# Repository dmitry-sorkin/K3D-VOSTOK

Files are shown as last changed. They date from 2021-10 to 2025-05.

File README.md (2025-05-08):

# K3D VOSTOK

Проект продвинутого крупногабаритного IDEX принтера.

Когда-то проект выкладывался на GitHub. Но после событий 2022 года использовать эту платформу стало небезопасно для проекта. В связи с этим, релизы, моды и багртрекер проекта теперь располагаются на собственном сайте:

- [Релизы](https://forum.k3d.tech/c/vostok-releases/21)
- [Модификации](https://forum.k3d.tech/c/vostok-mods/17)
- [Багтрекер](https://forum.k3d.tech/c/vostok-bugtracker/19)

Возвращение на GitHub не планируется. По крайней мере пока сохраняется возможность блокировки репозитория из-за не зависящих от автора проекта обстоятельств.

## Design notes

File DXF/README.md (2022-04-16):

# DXF Generator

DXF Generator сделан для генерирования DXF чертежей зашивки.

❗ Alpha-test ❗

На данный момент принтер и документация к нему находятся на стадии активного проектирования. Автор не гарантирует вам ничего. Все результаты работы всех калькуляторов, генераторов и т.д. стоит дважды перепроверить перед совершением заказа.

## Контакты:

+ Создатель: Дмитрий Соркин [dbsorkin@gmail.com]
+ Новости проекта: [https://t.me/vostok3dp]
+ Обсуждение проекта: [https://t.me/k3d_vostok]

## Как поучаствовать в проекте?:

Собрать и тестировать. Большая часть багов может быть найдена только при реальной эксплуатации принтера.

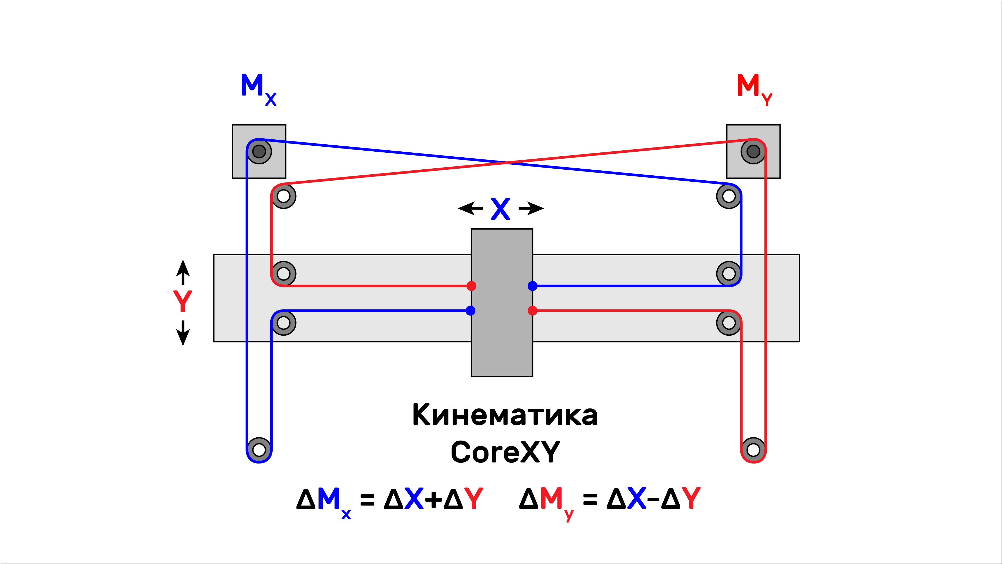
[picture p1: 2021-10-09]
Docs/kinematics_CoreXY.jpg

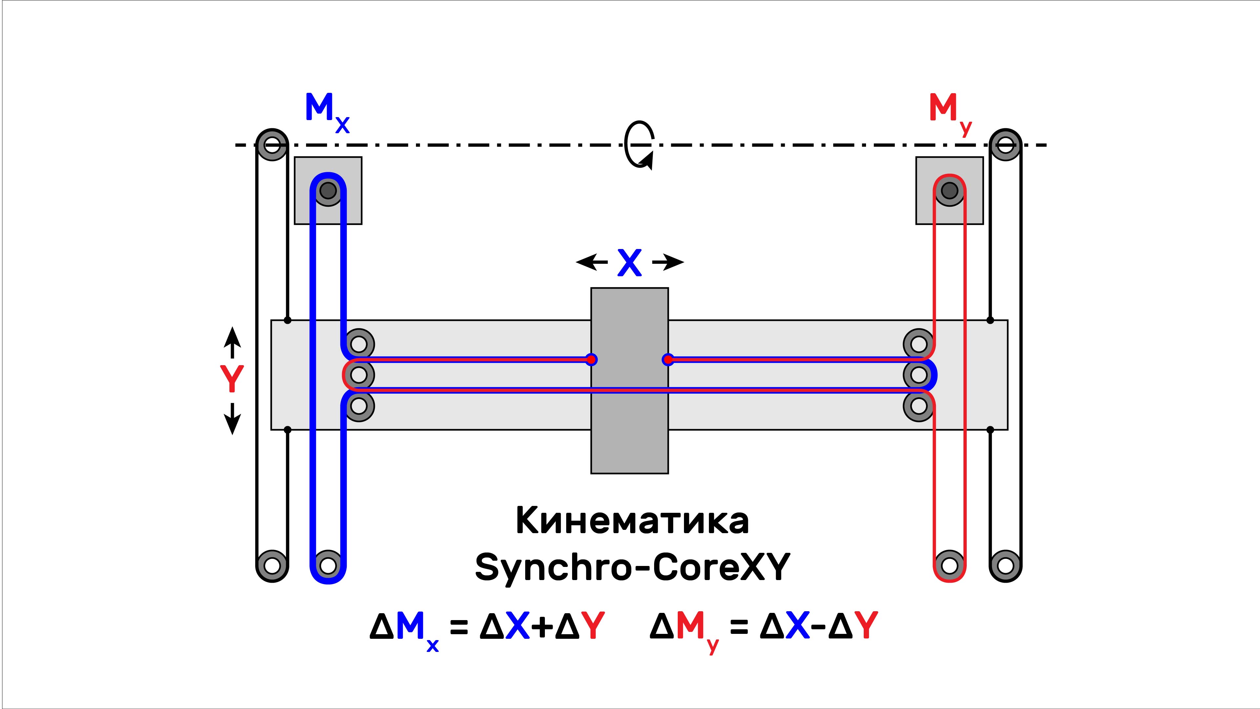
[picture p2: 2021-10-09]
Docs/kinematics_Synchro-CoreXY.jpg

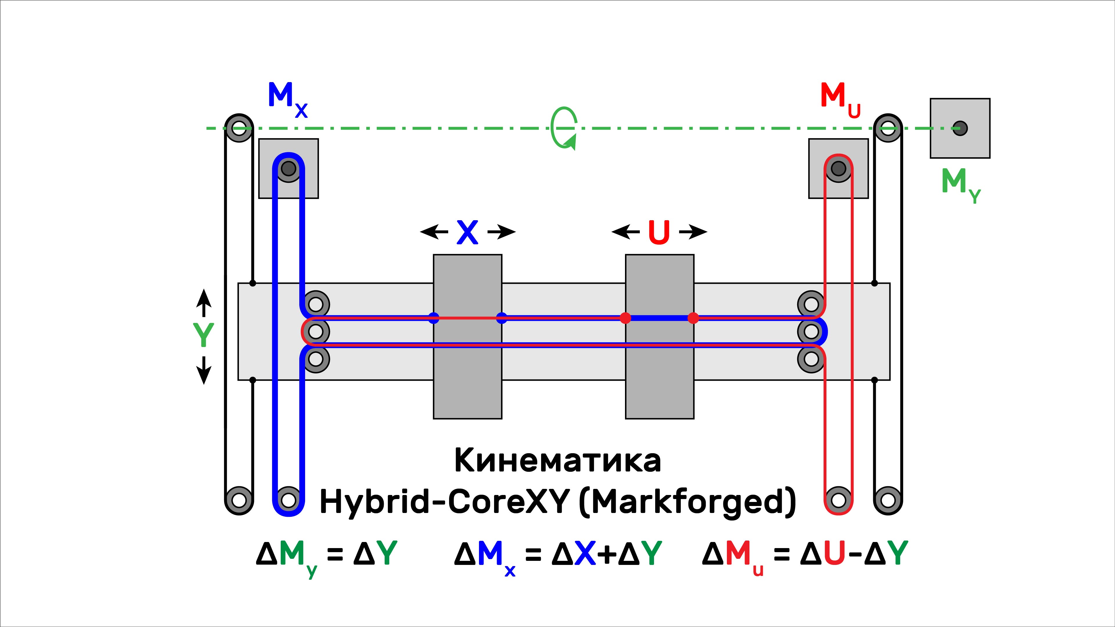
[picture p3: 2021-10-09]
Docs/kinematics_Hybrid-CoreXY.jpg

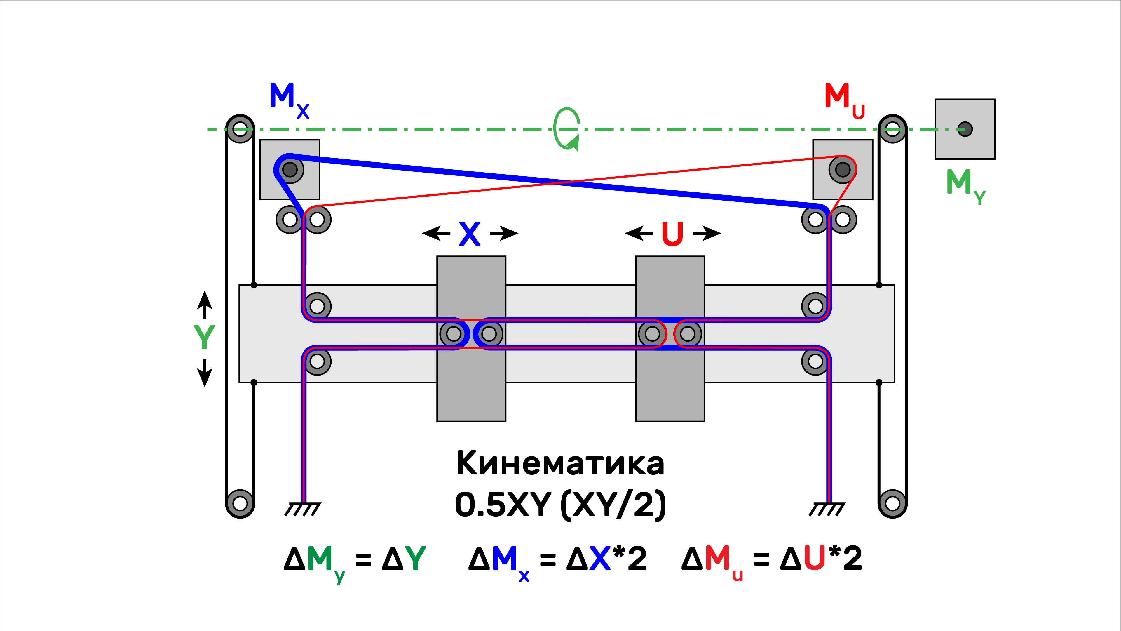
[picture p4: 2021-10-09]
Docs/kinematics_0.5XY.jpg

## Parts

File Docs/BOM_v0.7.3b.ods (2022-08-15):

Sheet: Настройки
Параметр | Значение | Примечание
Экструдер
Количество экструдеров | 2 | 1 — обычный одиночный экструдер. Доступны все кинематики 2 — IDEX. Доступны кинематики 0.5XY и Hybrid-CoreXY
Подающий механизм | K3D Minifeeder | Легкий и дешевый подающий механизм на основе деталей BMG. Используется в легкой печатающей голове (lightweight print head)
Хотэнд | Высокопроизводительный | Простой и дешевый универсальный хотэнд на основе хитблока E3D Volcano. Макс. Объёмный расход до 20-22мм³/с.
Ось Z
Желаемая область печати по Х | 400 мм | Определяет размер плиты стола и полный размер области печати по оси Х в миллиметрах
Желаемая область печати по Y | 250 мм | Определяет размер области печати по оси Y. Обратите внимание, что ввиду конструктивных особенностей принтера, размер плиты должен быть больше на 50мм (это будет автоматически расчитано на листе «покупные изделия»). Припуск в 50мм нужен для расположения крепежных отверстий, прищепок стекла, а также совместимости разных печатающих голов между собой.
Желаемая область печати по Z | 250 мм | Желаемая высота области печати по оси Z в миллиметрах. Реальный размер области печати будет немного больше для обеспечения ровного размера ходового винта
Количество точек крепления стола | 6 | Количество подпружиненных точек крепления стола. Для вариантов с 2 стойками Z доступно либо 4, либо 6 точек. Для вариантов с 4 стойками доступно 4, 6, 8 и 9 точек
Количество стоек оси Z | 2 | Количество стоек и приводов оси Z зависит от габарита области печати, но по желанию может быть скорректировано. Рекомендуется: При Y меньше 300 мм: 2 стойки и 2 привода При Y от 300 до 400 мм: 4 стойки и 2 привода При Y больше 400 мм: 4 стойки и 4 привода
Количество приводов оси Z | 2
Электроника
Материнская плата | BTT Octopus | Fysetc Spider, BTT Octopus подходят для всех версий VOSTOK и являются рекомендуемыми платами BTT Octopus Pro подходит для всех версий и рекомендуется для установки высоковольтных драйверов BTT SKR 3 подходит только для одноэкструдерной версии
Управляющая плата | Orange Pi 3 LTS | Управляющая плата для установки прошивки Klipper. Наиболее оптимальным вариантом по сочетанию цена/характеристики является Orange Pi 3 LTS
Печатные детали
Плотность филамента для несущих деталей | 1,08 г/см³ | Характеристики филамента, который будет использоваться для печати нагруженных деталей механики принтера (каретки, детали печатающей головы и т. д.). Рекомендуется использовать прочный, жесткий, термостойкий и хорошо спекающийся материал. Например: PP GF; PP GF30; PA12 GF30; PA6 GF30 и подобные. Плотность указывается в г/см³, цена в $/кг.
Стоимость филамента для несущих деталей | 2 700,00 ₽ | Стоимость килограмма филамента, из которого будут печататься основные несущие детали принтера
Плотность филамента для вспомогательных деталей | 1,28 г/см³ | Характеристики филамента, который будет использоваться для печати вспомогательных деталей (петли, держатели катушек и т. д.). Рекомендуется прочный, дешевый и легкий в печати филамент с термостойкостью от 70 градусов. Идеальным выбором будет PETG, но возможна замена. Плотность указывается в г/см³, цена в $/кг.
Стоимость филамента для вспомогательный деталей | 1 200,00 ₽ | Стоимость килограмма филамента, из которого будут печататься основные несущие детали принтера
Константы
Курс доллара | 60,00 ₽
Курс доллара Aliexpress | 68,00 ₽ | Используется для примерной корректировки стоимости деталей, покупаемых с Aliexpress
Вывод: Габариты принтера
Габарит принтера по X | 678 мм | Учтена толщина зашивки 4мм, купол и дверца отсека электроники. Не учтены головки винтов и дополнительное внешнее оборудование (внешние держатели катушек и т. д.)
Габарит принтера по Y | 504 мм
Габарит принтера по Z | 698 мм
Вывод: Стоимость
Покупные изделия | 34 442,40 ₽ | С рельсами KGT, для всех товаров не учтена стоимость доставки
Стандартные изделия | 7 360,02 ₽ | Самые дешевые винты, но качественные подшипники
Алюминиевый профиль | 5 993,16 ₽ | Учтен облегченный профиль. В случае использования полнотелого профиля цена выше на ~20%
Печатные детали | 3 069,83 ₽ | Без учёта вспомогательных структур

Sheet: Покупные изделия
На данном листе производится расчёт количества нестандартных деталей Ссылки указаны на проверенные товары с хорошим качеством. Единственное исключение — рельсы MGN9, MGN12 и каретки к ним. Так как качественные рельсы (HIWIN и т. п.) не продаются на Aliexpress, то указаны ссылки на значительно более дешевые KGT. У многих пользователей эти рельсы работают нормально, но в целом количество брака достаточно велико. Поэтому рекомендуется заказывать рельсы HIWIN у официального поставщика в вашем регионе. Ссылки на большую часть товаров являются аффилиативными. Покупая по ним вы поддерживаете проект.
Наименование | Удельная стоимость | Длина/площадь | Единиц | Общая стоимость | Ссылки | Альт. Ссылка | Примечание
Экструдер
Подающий механизм
Клон BMG | 622,00 ₽ |  | 2 | 1 244,00 ₽ | AE (http://alii.pub/6fdbrk) |  | Либо используется как есть, либо служит донором деталей для BeMeGe или Minifeeder
LGX Lite | 3 420,00 ₽ |  | 0 | 0,00 ₽ | BTech (https://www.bondtech.se/product/lgx-lite-extruder-no-motor/) |  | На данный момент продаётся только в Швеции. Если не можете купить, то рекомендуется замена на Minifeeder
Matrix Lite | 5 662,00 ₽ |  | 0 | 0,00 ₽ | AE (http://alii.pub/6fdbp1) |  | Идёт в комплекте с мотором, хитблоком v6, медным соплом v6, термистором, нагревательным элементом и вентилятором
Мотор Nema17 20-23мм | 672,00 ₽ |  | 0 | 0,00 ₽ | AE (http://alii.pub/6fdbno) |  | Для вариантов с BMG или BeMeGe. 1.8 градуса/шаг, любой производитель, любой удобный вам тип проводки
Мотор Nema14 20мм | 1 440,00 ₽ |  | 2 | 2 880,00 ₽ | AE (http://alli.pub/6fdf35) |  | Для вариантов с LGX Lite или Minifeeder. Обязательна запрессованная на вал мотора 10-зубая шестерня. Избегайте моторов 17мм так как у них не хватает крутящего момента, что ведёт к уменьшению производительности экструдера на ~10%
Хотэнд | 0,00 ₽
Радиатор e3d v6 | 83,00 ₽ |  | 0 | 0,00 ₽ | AE (http://alii.pub/6fdbsj) |  | Для головы с BMG используется как есть. Для облегченной печатающей головы необходима доработка
Радиатор CR-10 | 155,00 ₽ |  | 2 | 310,00 ₽ | AE (http://alii.pub/6fdbv2) |  | Используется для сборки в IDEX так как имеет регулировку сопла по высоте
Термобарьер e3d v6 биметалл | 266,00 ₽ |  | 0 | 0,00 ₽ | AE (http://alii.pub/6fdblx) |  | Титановый цельнометаллический как оптимум цена/качество. Биметалл сталь+медь для максимальных характеристик
Термобарьер CR-10 биметалл | 266,00 ₽ |  | 2 | 532,00 ₽ | AE (http://alii.pub/6fdblx) |  | Цельнометаллический титановый нельзя так как эффективности радиатора не хватит. Только биметалл
Хитблок e3d v6 | 88,00 ₽ |  | 0 | 0,00 ₽ | AE (http://alii.pub/6f67wx) |  | Алюминиевые хитблоки — оптимум по цена/масса/качество. Медные, латунные и так далее не нужны. Обратите внимание, что если хитблок включен в комплект поставки экструдера или хотэнда, то покупать его не надо
Хитблок e3d volcano | 149,00 ₽ |  | 2 | 298,00 ₽ | AE (http://alii.pub/6fdbl5)
Хитблок CHC Pro | 1 525,00 ₽ |  | 0 | 0,00 ₽ | AE (http://alii.pub/6fdbw8) |  | Медно-керамический хитблок с повышенной производительностью. Имеет встроенный нагреватель и термистор
Сопло e3d v6 | 205,00 ₽ |  | 0 | 0,00 ₽ | AE (http://alii.pub/6fdbq0) | AE (http://alii.pub/6fdbq7) | Для печати монофиламентами лучше всего латунные сопла. Для печати композитами закалённые стальные
Сопло e3d volcano | 155,00 ₽ |  | 2 | 310,00 ₽ | AE (http://alii.pub/6f6ep5) | AE (http://alii.pub/6fdbkd)
Термистор | 144,00 ₽ |  | 2 | 288,00 ₽ | AE (http://alii.pub/6f67vr) |  | Для печати до 300°C лучше всего 104GT-2. Для печати на температурах выше 300°C — pt100, pt1000 и подобные
Нагревательный элемент 24в 40Вт | 130,00 ₽ |  | 2 | 260,00 ₽ | AE (http://alli.pub/6fdf1z) |  | Для обычных хотэндов 40Вт нагреватель безопаснее всего так как он не может расплавить хитблок.
Система охлаждения | 0,00 ₽
Вентилятор 5015 12-24в | 287,50 ₽ |  | 4 | 1 150,00 ₽ | AE (http://alli.pub/6fdf5h) |  | Вентилятор должен обязательно поддерживать ШИМ, иначе не будет возможности регулировать охлаждение
Вентилятор 4010 12-24в | 299,00 ₽ |  | 2 | 598,00 ₽ | DNS (https://www.dns-shop.ru/product/4a841272207ce478/ventilator-deepcool-xfan-40-dp-fdc-xf40/) | DNS (https://www.dns-shop.ru/product/dc21803bc4a23332/ventilator-fractal-design-silent-series-r3-40-fd-fan-ssr3-40-wt/)
Вентилятор 4007 12-24в | 390,00 ₽ |  | 0 | 0,00 ₽ | AE (http://alli.pub/6fdgoi) |  | Может быть заменен на 4010 вентилятор, но немного уменьшится область печати
Трубка PTFE ID2 OD4 | 0,20 ₽ | 630 мм | 2 | 252,00 ₽ | AE (http://alli.pub/6fdgs0) |  | Для подвода прутка от катушек к экструдерам и сборки хотэнда. Длина расчитана грубо, брать с запасом
Магнит D10 L1 | 8,25 ₽ |  | 0 | 0,00 ₽ | MM (https://mirmagnitov.ru/product/neodimovyy-magnit-disk-10kh1-mm-s-kleevym-sloem/) |  | Для крепления вентилятора обдува модели к каретке старой печатной головы. Можно заменить соединение на клеевое
Ось X | 0,00 ₽
Рельса MGN9 | 1,12 ₽ | 520 мм | 1 | 582,40 ₽ | AE (http://alli.pub/6fdguc) |  | Цена и ссылка указаны на рельсы KGT, имеющие случайное качество. Рекомендуется покупать рельсы HIWIN у официального поставщика в вашем регионе
Каретка MGN9H | 363,00 ₽ |  | 2 | 726,00 ₽ | AE (http://alli.pub/6fdguc)
Мотор Nema17; 38-60мм | 755,00 ₽ |  | 2 | 1 510,00 ₽ | AE (http://alli.pub/6fdh0r) |  | На принтер со столом 400х250 мотора 38мм хватает с запасом. На очень большие принтеры можно взять мотор больше
Шкив 2GT; вн.диам. 5 мм; 20 зубов | 274,00 ₽ |  | 2 | 548,00 ₽ | AE (http://alli.pub/6fdh4g)
Ремень 2GT; 9-10мм | 0,17 ₽ | 2910 мм | 2 | 960,30 ₽ | AE (http://alii.pub/6fdbfp) |  | Указана длина одного куска и количество таких кусков. Размер расчитывается грубо, обязательно брать с запасом
Ось Y | 0,00 ₽
Рельса MGN12 | 1,38 ₽ | 300 мм | 2 | 828,00 ₽ | AE (http://alli.pub/6fdguc) |  | Цена и ссылка указаны на рельсы KGT, имеющие случайное качество. Рекомендуется покупать рельсы HIWIN у официального поставщика в вашем регионе
Каретка MGN12H | 424,00 ₽ |  | 2 | 848,00 ₽ | AE (http://alli.pub/6fdguc)
Мотор Nema17; 38-60мм | 755,00 ₽ |  | 1 | 755,00 ₽ | AE (http://alli.pub/6fdh0r) |  | На принтер со столом 400х250 мотора 38мм хватает. На очень большие принтеры можно взять мотор больше
Вал диаметр 8 мм | 0,80 ₽ | 620 мм | 1 | 496,00 ₽ | AE (http://alli.pub/6fdhks)
Шкив 2GT; вн.диам. 5 мм; 20 зубов | 274,00 ₽ |  | 1 | 274,00 ₽ | AE (http://alli.pub/6fdh4g)
Шкив 2GT; вн.диам. 8 мм; 20 зубов | 274,00 ₽ |  | 3 | 822,00 ₽ | AE (http://alli.pub/6fdh4g)
Ремень 2GT; 9-10мм; открытый | 0,17 ₽ | 740 мм | 2 | 244,20 ₽ | AE (http://alii.pub/6fdbfp) |  | Длина ремня расчитывается грубо. Обязательно брать с запасом
Ремень 2GT; 9-10мм; кольцо 150мм (75 зубов) | 480,00 ₽ |  | 1 | 480,00 ₽ | AE (http://alli.pub/6fdhg4)
Ось Z | 0,00 ₽
Каретка Openbuilds в сборе | 296,00 ₽ |  | 2 | 592,00 ₽ | AE (http://alli.pub/6fdhys) |  | Продаётся с 4 колёсами, но нужно только 3. Лишнее в запчасти
Винт Tr8x2 | 1,16 ₽ | 300 мм | 2 | 696,00 ₽ | AE (http://alli.pub/6fdi93) |  | Tr8x2 — однозаходная трапецеидальная резьба. Диаметр = 8мм. Ход = шаг = 2мм.
Гайка POM Tr8x2 | 114,00 ₽ |  | 2 | 228,00 ₽ | AE (http://alli.pub/6fdid6) |  | Tr8x2 — резьба трапецеидальная с диаметром 8мм и шагом 2мм. Ход равен шагу.
Мотор Nema17; 30-42мм | 755,00 ₽ |  | 2 | 1 510,00 ₽ | AE (http://alli.pub/6fdh0r) |  | Можно поставить моторы длиннее, но придется поднимать принтер на ножках
Муфта жесткая 5x8мм | 93,00 ₽ |  | 2 | 186,00 ₽ | AE (http://alii.pub/6fdb9h) |  | Можно заменить на кулачковую или печатную
Стол | 0,00 ₽
Лист алюминиевый 400 х 300 х 4 мм | 8 000,00 ₽ | 0,12 м² | 1 | 960,00 ₽ | Prutki (http://prutki.ru/list-alyuminievyj-amg2-tolshchina-4-mm/) |  | Можно заменить на латунь или стеклотекстолит
Грелка силиконовая 400 х 250 мм | 16 700,00 ₽ | 0,1 м² | 1 | 1 670,00 ₽ | AE (http://alli.pub/6fdk03) | AE (http://alli.pub/6fdk4d) | Желательно брать от проверенного проивзодителя ради безопасности
Стекло 400 х 300 х 4 мм | 2 000,00 ₽ | 0,12 м² | 1 | 240,00 ₽ | N/A | N/A | Обычное оконное стекло из ближайшей стеклорезки
Прищепка для стекла | 25,00 ₽ |  | 4 | 100,00 ₽ | AE (http://alli.pub/6fdkaz)
Пружина OD8 L25 | 12,00 ₽ |  | 6 | 72,00 ₽ | AE (http://alli.pub/6fdosk)
Электроника | 0,00 ₽
Блок питания 24в 200Вт | 2 250,00 ₽ |  | 1 | 2 250,00 ₽ | CD (https://www.chipdip.ru/product/lrs-200-24) |  | Качественный блок питания с пассивным охлаждением
Блок питания 24в 350Вт | 3 340,00 ₽ |  | 0 | 0,00 ₽ | CD (https://www.chipdip.ru/product/lrs-350-24) |  | Качественный блок питания с активным и шумным охлаждением. Придётся менять вентилятор в нём на тихий
Блок питания 5в 25Вт | 940,00 ₽ |  | 0 | 0,00 ₽ | CD (https://www.chipdip.ru/product/rs-25-5) |  | На случай, если 5в линии питания материнской платы не будет хватать для питания управляющей платы
Вентилятор 90-120 мм 12 в | 389,00 ₽ |  | 0 | 0,00 ₽ | DNS (https://www.dns-shop.ru/product/0b8ea57aad253332/ventilator-xilence-xf038-xpf92r/) |  | Для замены вентилятора в блоке питания LRS-350
Fysetc Spider + 8x tmc2209 | 4 600,00 ₽ |  | 0 | 0,00 ₽ | AE (http://alli.pub/6fdksh)
BTT Octopus + 8x tmc2209 | 4 234,00 ₽ |  | 1 | 4 234,00 ₽ | AE (http://alli.pub/6fdkrb)
BTT Octopus Pro + 8x tmc2209 | 5 775,00 ₽ |  | 0 | 0,00 ₽ | AE (http://alli.pub/6fdkn8)
BTT SKR 1.4 + 5x tmc2209 | 3 270,00 ₽ |  | 0 | 0,00 ₽ | AE (http://alli.pub/6fdkn8)
Orange Pi Lite | 1 853,00 ₽ |  | 0 | 0,00 ₽ | AE (http://alli.pub/6fdkvl)
Orange Pi 3 LTS | 2 403,00 ₽ |  | 1 | 2 403,00 ₽ | AE (http://alii.pub/6fdbj0)
Orange Pi 4 LTS | 5 005,00 ₽ |  | 0 | 0,00 ₽ | AE (http://alli.pub/6fdkum)
Карта памяти microSD 16Gb | 599,00 ₽ |  | 1 | 599,00 ₽ | DNS (https://www.dns-shop.ru/product/b7ef4eb6147c3332/karta-pamati-smartbuy-microsdhc-8-gb-sb8gbsdcl10-00/)
Реле твердотельное 25А | 195,00 ₽ |  | 1 | 195,00 ₽ | AE (http://alli.pub/6fdkwk)
Концевик оптический | 62,00 ₽ |  | 2 | 124,00 ₽ | AE (http://alli.pub/6fdkg8)
Концевик механический | 9,50 ₽ |  | 2 | 19,00 ₽ | AE (http://alli.pub/6fdkwy) |  | С лапкой со скруглением или роликом на конце. Если не хотите использовать sensorless homing на оси Y, то добавьте еще 2
Розетка 250В | 153,00 ₽ |  | 1 | 153,00 ₽ | AE (http://alli.pub/6fdkdi)
Зашивка и навесное | 0,00 ₽
Вентилятор 200мм | 999,00 ₽ |  | 1 | 999,00 ₽ | DNS (https://www.dns-shop.ru/product/da7f8125c4923332/ventilator-aerocool-duo-20/)
Магнит D10 L1 | 8,25 ₽ |  | 2 | 16,50 ₽ | MM (https://mirmagnitov.ru/product/neodimovyy-magnit-disk-10kh1-mm-s-kleevym-sloem/)
Итого: |  |  |  | 34 442,40 ₽

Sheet: Стандартные изделия
 |  |  |  |  |  |  |  | Наименование сборки | K3D VOSTOK | XY portal | X axis | Y axis carriage | Roller | BMG print head | Matrix print head | Lite print head | X axis drive | Y axis drive | Left belt tensioner | Belt tensioner (roller) | Belt tensioner (fixed) | Right belt tensioner | X axis mechanical endstop | Y axis mechanical endstop | Lower frame | Z axis | Z axis guide | Z axis drive | Heatbed frame | Bed arm | Heatbed install | Optical endstop install | Optical endstop trigger | Quad guide nut install | Enclosure | Front door | Enclosure hinge | Back door | Back door lock | Electronics | Additions | Inner spool holder | Inner spool holder rocker | Enclosure top | Enclosure top hinge
 |  |  |  |  |  |  |  | Ед. | 1 | 1 | 1 | 2 | 19 | 0 | 0 | 2 | 2 | 1 | 1 | 2 | 2 | 1 | 2 | 1 | 1 | 1 | 2 | 2 | 1 | 3 | 1 | 1 | 1 | 0 | 1 | 2 | 6 | 1 | 2 | 1 | 1 | 2 | 4 | 2 | 2
Наименование | Стандарт | Резьба | Цена/ед. | Кол-во | Цена всего | Ссылки | Ссылка
Винт с полукруглой головкой и шестигранным углублением под ключ | ISO 7380-1 | М3х6 | 3,00 ₽ | 172 | 516,00 ₽ | krepcom (https://krepcom.ru/catalog/vinty-razdel/vint_3kh6_s_polukrugloy_golovkoy_i_vnutrennim_shestigrannikom_din_7380_nerzh_stal_a2.htm) | krep-shop (https://krep-shop.ru/katalog/bolty_i_vinty/iso_7380_1/3kh6_v_sh_p_kr_nerzh_a2_iso_7380/) |  |  |  |  | 2 |  | 4 | 10 | 6 | 3 | 8 |  |  |  |  |  |  |  |  |  |  |  |  |  |  | 2 |  |  | 2 |  |  |  |  |  |  |  | 68
 | ISO 7380-1 | М3х12 | 3,00 ₽ | 14 | 42,00 ₽ | krepcom (https://krepcom.ru/catalog/vinty-razdel/vint_3kh12_s_polukrugloy_golovkoy_i_vnutrennim_shestigrannikom_din_7380_nerzh_stal_a2.htm) | krep-shop (https://krep-shop.ru/katalog/bolty_i_vinty/iso_7380_1/3kh12_v_sh_p_kr_nerzh_a2_iso_7380/) |  |  |  |  |  |  |  |  | 2 |  |  |  |  |  |  |  |  |  |  |  | 4 |  |  |  |  |  | 4 |  |  |  |  | 1
 | ISO 7380-1 | М3х16 | 4,00 ₽ | 0 | 0,00 ₽ | krepcom (https://krepcom.ru/catalog/vinty-razdel/vint_3kh16_s_polukrugloy_golovkoy_i_vnutrennim_shestigrannikom_din_7380_nerzh_stal_a2.htm) | krep-shop (https://krep-shop.ru/katalog/bolty_i_vinty/iso_7380_1/3kh16_v_sh_p_kr_nerzh_a2_iso_7380/) |  |  |  |  |  |  | 2
 | ISO 7380-1 | М4х8 | 5,00 ₽ | 47 | 235,00 ₽ | krepcom (https://krepcom.ru/catalog/vinty-razdel/vint_4kh8_s_polukrugloy_golovkoy_i_vnutrennim_shestigrannikom_din_7380_nerzh_stal_a2.htm) | krep-shop (https://krep-shop.ru/katalog/bolty_i_vinty/iso_7380_1/4kh8_v_sh_p_kr_nerzh_a2_iso_7380/) |  |  |  |  |  |  |  |  |  | 4 | 8 | 4 |  |  | 4 | 2 | 1 |  |  |  |  |  | 6
 | ISO 7380-1 | М4х12 | 5,00 ₽ | 22 | 110,00 ₽ | krepcom (https://krepcom.ru/catalog/vinty-razdel/vint_4kh12_s_polukrugloy_golovkoy_i_vnutrennim_shestigrannikom_din_7380_nerzh_stal_a2.htm) | krep-shop (https://krep-shop.ru/katalog/bolty_i_vinty/iso_7380_1/4kh12_v_sh_p_kr_nerzh_a2_iso_7380/) |  |  |  |  |  |  |  |  |  |  |  |  |  |  |  |  |  |  |  | 3 | 2 |  |  |  |  |  |  |  |  |  |  |  |  |  | 4 |  | 2
 | ISO 7380-1 | М6х12 | 7,00 ₽ | 42 | 294,00 ₽ | krepcom (https://krepcom.ru/catalog/vinty-razdel/vint_6kh12_s_polukrugloy_golovkoy_i_vnutrennim_shestigrannikom_din_7380_nerzh_stal_a2.htm) | krep-shop (https://krep-shop.ru/katalog/bolty_i_vinty/iso_7380_1/6kh12_v_sh_p_kr_nerzh_a2_iso_7380/) |  | 34 |  |  |  |  |  |  |  |  |  |  |  |  |  |  |  | 4 |  |  |  |  |  |  |  |  |  | 4
-||- с прессшайбой | ISO 7380-2 | М4х8 | 3,00 ₽ | 201 | 603,00 ₽ | krepcom (https://krepcom.ru/catalog/vinty-razdel/vint_4kh8_s_polukrugloy_golovkoy_i_flantsem_9335_nerzh_stal_a2.htm) | krep-shop (https://krep-shop.ru/katalog/bolty_i_vinty/iso_7380w/4kh8_v_sh_p_kr_i_flanets_nerzh_a2_iso_7380_mf/) |  |  |  |  |  |  |  |  |  |  |  |  |  |  |  |  |  |  |  |  |  |  |  |  |  |  |  | 201
Винт с потайной головкой и шестигранным углублением под ключ | DIN 7991 | М3х6 | 3,00 ₽ | 16 | 48,00 ₽ | krepcom (https://krepcom.ru/catalog/vinty-razdel/vint_3kh6_potay_s_vnutrennim_shestigrannikom_nerzhaveyka.htm) | krep-shop (https://krep-shop.ru/katalog/bolty_i_vinty/din_7991/3kh6_pot_v_sh_nerzh_a2_din_7991/) |  |  |  |  | 4 |  |  |  | 4
 | DIN 7991 | М3х12 | 3,00 ₽ | 16 | 48,00 ₽ | krepcom (https://krepcom.ru/catalog/vinty-razdel/vint_3kh12_potay_s_vnutrennim_shestigrannikom_nerzhaveyka.htm) | krep-shop (https://krep-shop.ru/katalog/bolty_i_vinty/din_7991/3kh12_pot_v_sh_nerzh_a2_din_7991/) |  |  |  |  | 2 |  |  |  |  |  |  |  |  |  |  |  |  |  |  |  |  |  |  |  |  |  |  |  |  | 2
 | DIN 7991 | М3х16 | 4,00 ₽ | 13 | 52,00 ₽ | krepcom (https://krepcom.ru/catalog/vinty-razdel/vint_potay_s_vnutrennim_shestigrannikom_m3kh16_din_7991_iso_10642_klass_prochnosti_10_9_otsinkovanny.htm) | krep-shop (https://krep-shop.ru/katalog/bolty_i_vinty/din_7991/3kh16_pot_v_sh_nerzh_a2_din_7991/) |  |  |  |  |  |  |  |  |  |  | 1 |  |  |  |  |  |  |  |  |  |  |  |  |  |  |  |  |  |  | 2
 | DIN 7991 | М3х20 | 5,00 ₽ | 8 | 40,00 ₽ | krepcom (https://krepcom.ru/catalog/vinty-razdel/vint_potay_s_vnutrennim_shestigrannikom_m3kh20_din_7991_iso_10642_klass_prochnosti_10_9_otsinkovanny.htm) | krep-shop (https://krep-shop.ru/katalog/bolty_i_vinty/din_7991/3kh20_pot_v_sh_nerzh_a2_din_7991/) |  |  |  |  |  |  |  | 3 |  |  |  |  | 1 |  |  |  |  |  |  |  |  |  |  |  |  |  |  |  |  | 1
 | DIN 7991 | М3х30 | 6,00 ₽ | 6 | 36,00 ₽ | krepcom (https://krepcom.ru/catalog/vinty-razdel/vint_potay_s_vnutrennim_shestigrannikom_3kh30_din_7991_otsinkovannyy.htm) | krep-shop (https://krep-shop.ru/katalog/bolty_i_vinty/din_7991/3kh30_pot_v_sh_nerzh_a2_din_7991/) |  |  |  |  |  |  |  |  |  |  |  |  |  |  |  |  |  |  |  |  |  |  |  |  |  |  |  |  |  |  | 4 |  |  |  |  |  |  | 1
 | DIN 7991 | М3х35 | 6,00 ₽ | 12 | 72,00 ₽ | krepcom (https://krepcom.ru/catalog/vinty-razdel/vint_potay_s_vnutrennim_shestigrannikom_din_7991_3x35_stal_a2.htm) | krep-shop (https://krep-shop.ru/katalog/bolty_i_vinty/din_7991/3kh35_pot_v_sh_nerzh_a2_din_7991/) |  |  |  |  | 2 |  | 2 | 2 | 2 | 2
 | DIN 7991 | М3х50 | 10,00 ₽ | 6 | 60,00 ₽ | krepcom (https://krepcom.ru/catalog/vinty-razdel/vint_potay_3kh50_stal_a2.htm) | krep-shop (https://krep-shop.ru/katalog/bolty_i_vinty/din_7991/3kh50_pot_v_sh_nerzh_a2_din_7991/) |  |  |  |  |  |  |  |  |  |  |  |  |  |  |  |  |  |  |  |  |  |  |  | 6
 |  | М4х8 | 3,00 ₽ | 29 | 87,00 ₽ | krepcom (https://krepcom.ru/catalog/vinty-razdel/vint_potay_s_vnutrennim_shestigrannikom_m4kh8_din_7991_iso_10642_klass_prochnosti_10_9_otsinkovannyy.htm) | krep-shop (https://krep-shop.ru/katalog/bolty_i_vinty/din_7991/4kh8_pot_v_sh_nerzh_a2_din_7991/) |  |  |  |  |  |  |  |  |  | 2 | 4 |  |  |  |  |  |  |  |  | 6 |  |  | 2 |  | 3 |  | 4
 |  | М4х12 | 4,00 ₽ | 8 | 32,00 ₽ | krepcom (https://krepcom.ru/catalog/vinty-razdel/vint_potay_s_vnutrennim_shestigrannikom_m4kh12_din_7991_iso_10642_klass_prochnosti_10_9_otsinkovanny.htm) | krep-shop (https://krep-shop.ru/katalog/bolty_i_vinty/din_7991/4kh12_pot_v_sh_nerzh_a2_din_7991/) |  |  |  |  | 2 |  |  |  |  |  |  |  |  |  |  |  |  |  |  |  | 2
 |  | М5х12 | 4,00 ₽ | 24 | 96,00 ₽ | krepcom (https://krepcom.ru/catalog/vinty-razdel/vint_potay_5kh12_s_vnutrennim_shestigrannikom_otsinkovannyy.htm) | krep-shop (https://krep-shop.ru/katalog/bolty_i_vinty/din_7991/5kh12_pot_v_sh_nerzh_a2_din_7991/) |  |  |  |  |  |  |  |  |  |  |  |  |  |  |  |  |  |  |  |  |  |  |  |  |  |  |  |  |  |  |  |  |  |  |  | 6
 |  | М5х16 | 5,00 ₽ | 2 | 10,00 ₽ | krepcom (https://krepcom.ru/catalog/vinty-razdel/vint_potay_s_vnutrennim_shestigrannikom_m5kh16_din_7991_iso_10642_klass_prochnosti_10_9_otsinkovanny.htm) | krep-shop (https://krep-shop.ru/katalog/bolty_i_vinty/din_7991/5kh16_pot_v_sh_nerzh_a2_din_7991/) |  |  |  |  |  |  |  |  |  |  |  | 1 |  |  | 1
Винт с цилиндрической головкой и шестигранным углублением под ключ | DIN 912 | М2.5х8 | 5,00 ₽ | 0 | 0,00 ₽ | krepcom (https://krepcom.ru/catalog/bolty-razdel/bolt_vint_s_vnutrennim_shestigrannikom_i_tsilindricheskoy_golovkoy_din_912_2_5kh8_nerzhaveyka_a4.htm) | krep-shop (https://krep-shop.ru/katalog/bolty_i_vinty/din_912/2_5kh8_v_sh_nerzh_a2_din_912/) |  |  |  |  |  |  |  |  | 0
 |  | М3х8 | 2,00 ₽ | 56 | 112,00 ₽ | krepcom (https://krepcom.ru/catalog/vinty-razdel/vint_s_vnutrennim_shestigrannikom_3kh8_din_912_klass_10_9_otsinkovannyy.htm) | krep-shop (https://krep-shop.ru/katalog/bolty_i_vinty/din_912/3kh8_v_sh_nerzh_a2_din_912/) |  |  | 20 | 26 |  |  |  |  |  |  |  |  |  |  |  |  |  |  |  |  | 4 |  |  |  | 2
 |  | М3х20 | 5,00 ₽ | 10 | 50,00 ₽ | krepcom (https://krepcom.ru/catalog/bolty-razdel/bolt_imbus_3h20_nerj_DIN_912__stal__a2.htm) | krep-shop (https://krep-shop.ru/katalog/bolty_i_vinty/din_912/3kh20_v_sh_nerzh_a2_din_912/) |  |  |  |  |  |  |  |  | 2 |  | 2 |  |  | 2
 |  | М3х40 | 8,00 ₽ | 0 | 0,00 ₽ | krepcom (https://krepcom.ru/catalog/vysokoprochnyy_krepezh_12_9/vint_s_tsilindricheskoy_golovkoy_i_vnutrennim_shestigrannikom_din_912_3x40_vysokoprochnyy_12_9.htm) | krep-shop (https://krep-shop.ru/katalog/bolty_i_vinty/din_912/3kh40_v_sh_nerzh_a2_din_912/) |  |  |  |  |  |  | 3
 |  | М5х16 | 4,00 ₽ | 2 | 8,00 ₽ | krepcom (https://krepcom.ru/catalog/bolty-razdel/vint_bolt_din_912_m5kh16_klass_prochnosti_8_8.htm) | krep-shop (https://krep-shop.ru/katalog/bolty_i_vinty/din_912/5kh16_v_sh_nerzh_a2_din_912/) |  |  |  |  |  |  |  |  |  |  |  |  |  | 1
Болт | DIN 933 | М5х50 | 4,00 ₽ | 4 | 16,00 ₽ | krepcom (https://krepcom.ru/catalog/bolty-razdel/bolt_shestigrannyy_5kh50_din_933_klass_prochnosti_8_8_otsinkovannyy.htm) | krep-shop (https://krep-shop.ru/katalog/bolty_i_vinty/din_933/5kh50_nerzh_a2_din_933/) |  |  |  |  |  |  |  |  |  |  |  |  | 1 | 1
Гайка шестигранная | DIN 934 | М3 | 2,00 ₽ | 56 | 112,00 ₽ | krepcom (https://krepcom.ru/catalog/gayki-razdel/gayka_sh_gr_m_3_DIN_934_ots.htm) | krep-shop (https://krep-shop.ru/katalog/gaiki/din_934/m3_nerzh_a_2_din_934/) |  |  |  |  | 4 |  | 6 | 2 |  | 2 |  |  |  |  |  |  |  |  |  |  |  |  |  | 6 |  |  |  |  |  | 4 | 4 |  |  |  |  |  |  | 5
 |  | М4 | 2,00 ₽ | 6 | 12,00 ₽ | krepcom (https://krepcom.ru/catalog/gayki-razdel/gayka_sh_gr_m_4_DIN_934_ots.htm) | krep-shop (https://krep-shop.ru/katalog/gaiki/din_934/m4_nerzh_a_2_din_934/) |  |  |  |  |  |  |  |  |  |  |  |  |  |  |  |  |  |  |  | 3
 |  | М5 | 2,00 ₽ | 4 | 8,00 ₽ | krepcom (https://krepcom.ru/catalog/gayki-razdel/gayka_vysokoprochnaya_m5_din_934_klass_10_otsinkovannaya.htm) | krep-shop (https://krep-shop.ru/katalog/gaiki/din_934/m5_nerzh_a_2_din_934/) |  |  |  |  |  |  |  |  |  |  |  |  | 1 | 1
Т-гайка |  | М3 | 5,90 ₽ | 46 | 271,40 ₽ |  | AE (https://aliclick.shop/s/98tdf1) |  |  | 20 | 26
 |  | М4 | 5,90 ₽ | 283 | 1 669,70 ₽ |  | AE (https://aliclick.shop/s/98tdf1) |  |  |  |  | 2 |  |  |  |  | 4 | 12 | 4 |  |  | 4 | 2 | 1 |  |  | 6 | 3 |  | 8 |  | 3 |  | 4 | 201
Резьбовая вставка |  | М3х3 | 1,02 ₽ | 8 | 8,16 ₽ |  | AE (https://aliclick.shop/s/wmicc9) |  |  |  |  |  |  |  |  | 4
 |  | М3х5 | 2,23 ₽ | 22 | 49,06 ₽ |  | AE (https://aliclick.shop/s/wmicc9) |  |  |  |  |  |  |  |  | 8 |  |  |  |  |  |  |  |  |  |  |  |  |  |  | 6
Шайба | DIN 125 | М3 | 2,00 ₽ | 0 | 0,00 ₽ | krepcom (https://krepcom.ru/catalog/shayby/shayba-ploskaya-m3-din-125a-stal-nikelirovannaya.htm) | krep-shop (https://krep-shop.ru/katalog/shaiby/din_125/f3_2_m3_pl_nerzh_a2_din_125/)
 |  | М4 | 2,00 ₽ | 6 | 12,00 ₽ | krepcom (https://krepcom.ru/catalog/shayby/shayba-ploskaya-m4-din-125a-stal-nikelirovannaya.htm) | krep-shop (https://krep-shop.ru/katalog/shaiby/din_125/f4_3_m4_pl_nerzh_a2_din_125/) |  |  |  |  |  |  |  |  |  |  |  |  |  |  |  |  |  |  |  | 3
 |  | М8 | 2,00 ₽ | 3 | 6,00 ₽ | krepcom (https://krepcom.ru/catalog/shayby/shayba_m__8_prostaya_DIN_125_ots.htm) | krep-shop (https://krep-shop.ru/katalog/shaiby/din_125/f8_4_m8_pl_nerzh_a2_din_125/) |  |  |  |  |  |  |  |  |  |  | 3
Подшипник | 623 (zz или rs) |  | 33,50 ₽ | 19 | 636,50 ₽ |  | AE (https://aliclick.shop/s/ynp7je) |  |  |  |  |  | 1
 | F623 (zz или rs) |  | 31,10 ₽ | 38 | 1 181,80 ₽ |  | AE (https://aliclick.shop/s/fcdz1a) |  |  |  |  |  | 2
 | F695 (zz или rs) |  | 31,30 ₽ | 24 | 751,20 ₽ |  | AE (https://aliclick.shop/s/nh5fvo) |  |  |  |  |  |  |  |  |  |  |  |  |  |  |  |  |  |  |  |  |  |  |  |  |  |  |  |  |  |  |  |  |  |  |  | 6
 | F688 (zz или rs) |  | 37,60 ₽ | 2 | 75,20 ₽ |  | AE (https://aliclick.shop/s/db73tn) |  |  |  |  |  |  |  |  |  |  | 2
Итого: |  |  |  |  | 7 360,02 ₽
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

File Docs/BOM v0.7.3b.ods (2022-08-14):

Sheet: Настройки
Параметр | Значение | Примечание
Экструдер
Количество экструдеров | 2 | 1 — обычный одиночный экструдер. Доступны все кинематики 2 — IDEX. Доступны кинематики 0.5XY и Hybrid-CoreXY
Подающий механизм | K3D Minifeeder | Легкий и дешевый подающий механизм на основе деталей BMG. Используется в легкой печатающей голове (lightweight print head)
Хотэнд | Высокопроизводительный | Простой и дешевый универсальный хотэнд на основе хитблока E3D Volcano. Макс. Объёмный расход до 20-22мм³/с.
Ось Z
Желаемая область печати по Х | 400 мм | Определяет размер плиты стола и полный размер области печати по оси Х в миллиметрах
Желаемая область печати по Y | 250 мм | Определяет размер области печати по оси Y. Обратите внимание, что ввиду конструктивных особенностей принтера, размер плиты должен быть больше на 50мм (это будет автоматически расчитано на листе «покупные изделия»). Припуск в 50мм нужен для расположения крепежных отверстий, прищепок стекла, а также совместимости разных печатающих голов между собой.
Желаемая область печати по Z | 250 мм | Желаемая высота области печати по оси Z в миллиметрах. Реальный размер области печати будет немного больше для обеспечения ровного размера ходового винта
Количество точек крепления стола | 6 | Количество подпружиненных точек крепления стола. Для вариантов с 2 стойками Z доступно либо 4, либо 6 точек. Для вариантов с 4 стойками доступно 4, 6, 8 и 9 точек
Количество стоек оси Z | 2 | Количество стоек и приводов оси Z зависит от габарита области печати, но по желанию может быть скорректировано. Рекомендуется: При Y меньше 300 мм: 2 стойки и 2 привода При Y от 300 до 400 мм: 4 стойки и 2 привода При Y больше 400 мм: 4 стойки и 4 привода
Количество приводов оси Z | 2
Электроника
Материнская плата | BTT Octopus | Fysetc Spider, BTT Octopus подходят для всех версий VOSTOK и являются рекомендуемыми платами BTT Octopus Pro подходит для всех версий и рекомендуется для установки высоковольтных драйверов BTT SKR 3 подходит только для одноэкструдерной версии
Управляющая плата | Orange Pi 3 LTS | Управляющая плата для установки прошивки Klipper. Наиболее оптимальным вариантом по сочетанию цена/характеристики является Orange Pi 3 LTS
Печатные детали
Плотность филамента для несущих деталей | 1,08 г/см³ | Характеристики филамента, который будет использоваться для печати нагруженных деталей механики принтера (каретки, детали печатающей головы и т. д.). Рекомендуется использовать прочный, жесткий, термостойкий и хорошо спекающийся материал. Например: PP GF; PP GF30; PA12 GF30; PA6 GF30 и подобные. Плотность указывается в г/см³, цена в $/кг.
Стоимость филамента для несущих деталей | 2 700,00 ₽ | Стоимость килограмма филамента, из которого будут печататься основные несущие детали принтера
Плотность филамента для вспомогательных деталей | 1,28 г/см³ | Характеристики филамента, который будет использоваться для печати вспомогательных деталей (петли, держатели катушек и т. д.). Рекомендуется прочный, дешевый и легкий в печати филамент с термостойкостью от 70 градусов. Идеальным выбором будет PETG, но возможна замена. Плотность указывается в г/см³, цена в $/кг.
Стоимость филамента для вспомогательный деталей | 1 200,00 ₽ | Стоимость килограмма филамента, из которого будут печататься основные несущие детали принтера
Константы
Курс доллара | 60,00 ₽
Курс доллара Aliexpress | 68,00 ₽ | Используется для примерной корректировки стоимости деталей, покупаемых с Aliexpress
Вывод: Габариты принтера
Габарит принтера по X | 678 мм | Учтена толщина зашивки 4мм, купол и дверца отсека электроники. Не учтены головки винтов и дополнительное внешнее оборудование (внешние держатели катушек и т. д.)
Габарит принтера по Y | 504 мм
Габарит принтера по Z | 698 мм
Вывод: Стоимость
Покупные изделия | 34 442,40 ₽ | С рельсами KGT, для всех товаров не учтена стоимость доставки
Стандартные изделия | 7 360,02 ₽ | Самые дешевые винты, но качественные подшипники
Алюминиевый профиль | 3 915,16 ₽ | Учтен облегченный профиль. В случае использования полнотелого профиля цена выше на ~20%
Печатные детали | 3 069,83 ₽ | Без учёта вспомогательных структур
Проводка |  | Расчёт на данный момент не готов

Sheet: Покупные изделия
На данном листе производится расчёт количества нестандартных деталей Ссылки указаны на проверенные товары с хорошим качеством. Единственное исключение — рельсы MGN9, MGN12 и каретки к ним. Так как качественные рельсы (HIWIN и т. п.) не продаются на Aliexpress, то указаны ссылки на значительно более дешевые KGT. У многих пользователей эти рельсы работают нормально, но в целом количества брака достаточно велико. Поэтому рекомендуется заказывать рельсы HIWIN у официального поставщика в вашем регионе. Ссылки на большую часть товаров являются аффилиативными. Покупая по ним вы поддерживаете проект.
Наименование | Удельная стоимость | Длина/площадь | Единиц | Общая стоимость | Ссылки | Альт. Ссылка | Примечание
Экструдер
Подающий механизм
Клон BMG | 622,00 ₽ |  | 2 | 1 244,00 ₽ | AE (http://alii.pub/6fdbrk) |  | Либо используется как есть, либо служит донором деталей для BeMeGe или Minifeeder
LGX Lite | 3 420,00 ₽ |  | 0 | 0,00 ₽ | BTech (https://www.bondtech.se/product/lgx-lite-extruder-no-motor/) |  | На данный момент продаётся только в Швеции. Если не можете купить, то рекомендуется замена на Minifeeder
Matrix Lite | 5 662,00 ₽ |  | 0 | 0,00 ₽ | AE (http://alii.pub/6fdbp1) |  | Идёт в комплекте с мотором, хитблоком v6, медным соплом v6, термистором, нагревательным элементом и вентилятором
Мотор Nema17 20-23мм | 672,00 ₽ |  | 0 | 0,00 ₽ | AE (http://alii.pub/6fdbno) |  | Для вариантов с BMG или BeMeGe. 1.8 градуса/шаг, любой производитель, любой удобный вам тип проводки
Мотор Nema14 20мм | 1 440,00 ₽ |  | 2 | 2 880,00 ₽ | AE (http://alli.pub/6fdf35) |  | Для вариантов с LGX Lite или Minifeeder. Обязательна запрессованная на вал мотора 10-зубая шестерня. Избегайте моторов 17мм так как у них не хватает крутящего момента, что ведёт к уменьшению производительности экструдера на ~10%
Хотэнд | 0,00 ₽
Радиатор e3d v6 | 83,00 ₽ |  | 0 | 0,00 ₽ | AE (http://alii.pub/6fdbsj) |  | Для головы с BMG используется как есть. Для облегченной печатающей головы необходима доработка
Радиатор CR-10 | 155,00 ₽ |  | 2 | 310,00 ₽ | AE (http://alii.pub/6fdbv2) |  | Используется для сборки в IDEX так как имеет регулировку сопла по высоте
Термобарьер e3d v6 биметалл | 266,00 ₽ |  | 0 | 0,00 ₽ | AE (http://alii.pub/6fdblx) |  | Титановый цельнометаллический как оптимум цена/качество. Биметалл сталь+медь для максимальных характеристик
Термобарьер CR-10 биметалл | 266,00 ₽ |  | 2 | 532,00 ₽ | AE (http://alii.pub/6fdblx) |  | Цельнометаллический титановый нельзя так как эффективности радиатора не хватит. Только биметалл
Хитблок e3d v6 | 88,00 ₽ |  | 0 | 0,00 ₽ | AE (http://alii.pub/6f67wx) |  | Алюминиевые хитблоки — оптимум по цена/масса/качество. Медные, латунные и так далее не нужны. Обратите внимание, что если хитблок включен в комплект поставки экструдера или хотэнда, то покупать его не надо
Хитблок e3d volcano | 149,00 ₽ |  | 2 | 298,00 ₽ | AE (http://alii.pub/6fdbl5)
Хитблок CHC Pro | 1 525,00 ₽ |  | 0 | 0,00 ₽ | AE (http://alii.pub/6fdbw8) |  | Медно-керамический хитблок с повышенной производительностью. Имеет встроенный нагреватель и термистор
Сопло e3d v6 | 205,00 ₽ |  | 0 | 0,00 ₽ | AE (http://alii.pub/6fdbq0) | AE (http://alii.pub/6fdbq7) | Для печати монофиламентами лучше всего латунные сопла. Для печати композитами закалённые стальные
Сопло e3d volcano | 155,00 ₽ |  | 2 | 310,00 ₽ | AE (http://alii.pub/6f6ep5) | AE (http://alii.pub/6fdbkd)
Термистор | 144,00 ₽ |  | 2 | 288,00 ₽ | AE (http://alii.pub/6f67vr) |  | Для печати до 300°C лучше всего 104GT-2. Для печати на температурах выше 300°C — pt100, pt1000 и подобные
Нагревательный элемент 24в 40Вт | 130,00 ₽ |  | 2 | 260,00 ₽ | AE (http://alli.pub/6fdf1z) |  | Для обычных хотэндов 40Вт нагреватель безопаснее всего так как он не может расплавить хитблок.
Система охлаждения | 0,00 ₽
Вентилятор 5015 12-24в | 287,50 ₽ |  | 4 | 1 150,00 ₽ | AE (http://alli.pub/6fdf5h) |  | Вентилятор должен обязательно поддерживать ШИМ, иначе не будет возможности регулировать охлаждение
Вентилятор 4010 12-24в | 299,00 ₽ |  | 2 | 598,00 ₽ | DNS (https://www.dns-shop.ru/product/4a841272207ce478/ventilator-deepcool-xfan-40-dp-fdc-xf40/) | DNS (https://www.dns-shop.ru/product/dc21803bc4a23332/ventilator-fractal-design-silent-series-r3-40-fd-fan-ssr3-40-wt/)
Вентилятор 4007 12-24в | 390,00 ₽ |  | 0 | 0,00 ₽ | AE (http://alli.pub/6fdgoi) |  | Может быть заменен на 4010 вентилятор, но немного уменьшится область печати
Трубка PTFE ID2 OD4 | 0,20 ₽ | 630 мм | 2 | 252,00 ₽ | AE (http://alli.pub/6fdgs0) |  | Для подвода прутка от катушек к экструдерам и сборки хотэнда. Длина расчитана грубо, брать с запасом
Магнит D10 L1 | 8,25 ₽ |  | 0 | 0,00 ₽ | MM (https://mirmagnitov.ru/product/neodimovyy-magnit-disk-10kh1-mm-s-kleevym-sloem/) |  | Для крепления вентилятора обдува модели к каретке старой печатной головы. Можно заменить соединение на клеевое
Ось X | 0,00 ₽
Рельса MGN9 | 1,12 ₽ | 520 мм | 1 | 582,40 ₽ | AE (http://alli.pub/6fdguc) |  | Цена и ссылка указаны на рельсы KGT, имеющие случайное качество. Рекомендуется покупать рельсы HIWIN у официального поставщика в вашем регионе
Каретка MGN9H | 363,00 ₽ |  | 2 | 726,00 ₽ | AE (http://alli.pub/6fdguc)
Мотор Nema17; 38-60мм | 755,00 ₽ |  | 2 | 1 510,00 ₽ | AE (http://alli.pub/6fdh0r) |  | На принтер со столом 400х250 мотора 38мм хватает с запасом. На очень большие принтеры можно взять мотор больше
Шкив 2GT; вн.диам. 5 мм; 20 зубов | 274,00 ₽ |  | 2 | 548,00 ₽ | AE (http://alli.pub/6fdh4g)
Ремень 2GT; 9-10мм | 0,17 ₽ | 2910 мм | 2 | 960,30 ₽ | AE (http://alii.pub/6fdbfp) |  | Указана длина одного куска и количество таких кусков. Размер расчитывается грубо, обязательно брать с запасом
Ось Y | 0,00 ₽
Рельса MGN12 | 1,38 ₽ | 300 мм | 2 | 828,00 ₽ | AE (http://alli.pub/6fdguc) |  | Цена и ссылка указаны на рельсы KGT, имеющие случайное качество. Рекомендуется покупать рельсы HIWIN у официального поставщика в вашем регионе
Каретка MGN12H | 424,00 ₽ |  | 2 | 848,00 ₽ | AE (http://alli.pub/6fdguc)
Мотор Nema17; 38-60мм | 755,00 ₽ |  | 1 | 755,00 ₽ | AE (http://alli.pub/6fdh0r) |  | На принтер со столом 400х250 мотора 38мм хватает. На очень большие принтеры можно взять мотор больше
Вал диаметр 8 мм | 0,80 ₽ | 620 мм | 1 | 496,00 ₽ | AE (http://alli.pub/6fdhks)
Шкив 2GT; вн.диам. 5 мм; 20 зубов | 274,00 ₽ |  | 1 | 274,00 ₽ | AE (http://alli.pub/6fdh4g)
Шкив 2GT; вн.диам. 8 мм; 20 зубов | 274,00 ₽ |  | 3 | 822,00 ₽ | AE (http://alli.pub/6fdh4g)
Ремень 2GT; 9-10мм; открытый | 0,17 ₽ | 740 мм | 2 | 244,20 ₽ | AE (http://alii.pub/6fdbfp) |  | Длина ремня расчитывается грубо. Обязательно брать с запасом
Ремень 2GT; 9-10мм; кольцо 150мм (75 зубов) | 480,00 ₽ |  | 1 | 480,00 ₽ | AE (http://alli.pub/6fdhg4)
Ось Z | 0,00 ₽
Каретка Openbuilds в сборе | 296,00 ₽ |  | 2 | 592,00 ₽ | AE (http://alli.pub/6fdhys) |  | Продаётся с 4 колёсами, но нужно только 3. Лишнее в запчасти
Винт Tr8x2 | 1,16 ₽ | 300 мм | 2 | 696,00 ₽ | AE (http://alli.pub/6fdi93) |  | Tr8x2 — однозаходная трапецеидальная резьба. Диаметр = 8мм. Ход = шаг = 2мм.
Гайка POM Tr8x2 | 114,00 ₽ |  | 2 | 228,00 ₽ | AE (http://alli.pub/6fdid6) |  | Tr8x2 — резьба трапецеидальная с диаметром 8мм и шагом 2мм. Ход равен шагу.
Мотор Nema17; 30-42мм | 755,00 ₽ |  | 2 | 1 510,00 ₽ | AE (http://alli.pub/6fdh0r) |  | Можно поставить моторы длиннее, но придется поднимать принтер на ножках
Муфта жесткая 5x8мм | 93,00 ₽ |  | 2 | 186,00 ₽ | AE (http://alii.pub/6fdb9h) |  | Можно заменить на кулачковую или печатную
Стол | 0,00 ₽
Лист алюминиевый 400 х 300 х 4 мм | 8 000,00 ₽ | 0,12 м² | 1 | 960,00 ₽ | Prutki (http://prutki.ru/list-alyuminievyj-amg2-tolshchina-4-mm/) |  | Можно заменить на латунь или стеклотекстолит
Грелка силиконовая 400 х 250 мм | 16 700,00 ₽ | 0,1 м² | 1 | 1 670,00 ₽ | AE (http://alli.pub/6fdk03) | AE (http://alli.pub/6fdk4d) | Желательно брать от проверенного проивзодителя ради безопасности
Стекло 400 х 300 х 4 мм | 2 000,00 ₽ | 0,12 м² | 1 | 240,00 ₽ | N/A | N/A | Обычное оконное стекло из ближайшей стеклорезки
Прищепка для стекла | 25,00 ₽ |  | 4 | 100,00 ₽ | AE (http://alli.pub/6fdkaz)
Пружина OD8 L25 | 12,00 ₽ |  | 6 | 72,00 ₽ | AE (http://alli.pub/6fdosk)
Электроника | 0,00 ₽
Блок питания 24в 200Вт | 2 250,00 ₽ |  | 1 | 2 250,00 ₽ | CD (https://www.chipdip.ru/product/lrs-200-24) |  | Качественный блок питания с пассивным охлаждением
Блок питания 24в 350Вт | 3 340,00 ₽ |  | 0 | 0,00 ₽ | CD (https://www.chipdip.ru/product/lrs-350-24) |  | Качественный блок питания с активным и шумным охлаждением. Придётся менять вентилятор в нём на тихий
Блок питания 5в 25Вт | 940,00 ₽ |  | 0 | 0,00 ₽ | CD (https://www.chipdip.ru/product/rs-25-5) |  | На случай, если 5в линии питания материнской платы не будет хватать для питания управляющей платы
Вентилятор 90-120 мм 12 в | 389,00 ₽ |  | 0 | 0,00 ₽ | DNS (https://www.dns-shop.ru/product/0b8ea57aad253332/ventilator-xilence-xf038-xpf92r/) |  | Для замены вентилятора в блоке питания LRS-350
Fysetc Spider + 8x tmc2209 | 4 600,00 ₽ |  | 0 | 0,00 ₽ | AE (http://alli.pub/6fdksh)
BTT Octopus + 8x tmc2209 | 4 234,00 ₽ |  | 1 | 4 234,00 ₽ | AE (http://alli.pub/6fdkrb)
BTT Octopus Pro + 8x tmc2209 | 5 775,00 ₽ |  | 0 | 0,00 ₽ | AE (http://alli.pub/6fdkn8)
BTT SKR 1.4 + 5x tmc2209 | 3 270,00 ₽ |  | 0 | 0,00 ₽ | AE (http://alli.pub/6fdkn8)
Orange Pi Lite | 1 853,00 ₽ |  | 0 | 0,00 ₽ | AE (http://alli.pub/6fdkvl)
Orange Pi 3 LTS | 2 403,00 ₽ |  | 1 | 2 403,00 ₽ | AE (http://alii.pub/6fdbj0)
Orange Pi 4 LTS | 5 005,00 ₽ |  | 0 | 0,00 ₽ | AE (http://alli.pub/6fdkum)
Карта памяти microSD 16Gb | 599,00 ₽ |  | 1 | 599,00 ₽ | DNS (https://www.dns-shop.ru/product/b7ef4eb6147c3332/karta-pamati-smartbuy-microsdhc-8-gb-sb8gbsdcl10-00/)
Реле твердотельное 25А | 195,00 ₽ |  | 1 | 195,00 ₽ | AE (http://alli.pub/6fdkwk)
Концевик оптический | 62,00 ₽ |  | 2 | 124,00 ₽ | AE (http://alli.pub/6fdkg8)
Концевик механический | 9,50 ₽ |  | 2 | 19,00 ₽ | AE (http://alli.pub/6fdkwy) |  | С лапкой со скуглением или роликом на конце. Если не хотите использовать sensorless homing на оси Y, то добавьте еще 2
Розетка 250В | 153,00 ₽ |  | 1 | 153,00 ₽ | AE (http://alli.pub/6fdkdi)
Зашивка и навесное | 0,00 ₽
Вентилятор 200мм | 999,00 ₽ |  | 1 | 999,00 ₽ | DNS (https://www.dns-shop.ru/product/da7f8125c4923332/ventilator-aerocool-duo-20/)
Магнит D10 L1 | 8,25 ₽ |  | 2 | 16,50 ₽ | MM (https://mirmagnitov.ru/product/neodimovyy-magnit-disk-10kh1-mm-s-kleevym-sloem/)
Итого: |  |  |  | 34 442,40 ₽
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

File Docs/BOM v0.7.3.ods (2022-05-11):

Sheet: Настройки
Параметр | Значение |  | Примечание
Экструдер
Количество экструдеров | 2 |  | 1 — обычный одиночный экструдер. Доступны все кинематики 2 — IDEX. Доступны кинематики 0.5XY и Hybrid-CoreXY
Подающий механизм | K3D Minifeeder |  | Легкий и дешевый подающий механизм на основе деталей BMG. Используется в легкой печатающей голове (lightweight print head)
Хотэнд | Высокопроизводительный |  | Простой и дешевый универсальный хотэнд на основе хитблока E3D Volcano. Макс. Объёмный расход до 20-22мм³/с.
Ось Z
Желаемая область печати по Х | 400 мм |  | Определяет размер стола по оси Х в миллиметрах.
Желаемая область печати по Y | 250 мм |  | Определяет размер стола по оси Y. Обратите внимание, что ввиду конструктивный особенностей принтера, размер плиты будет увеличен на 50мм. Они не будут использоваться в печати, но в них будут крепежные элементы стола + в них можно будет сделать крепеж съёмного покрытия.
Желаемая область печати по Z | 250 мм |  | Желаемая высота области печати по оси Z в миллиметрах. Реальный размер области печати будет немного больше для обеспечения ровного размера ходового винта
Количество точек крепления стола | 6 |  | Количество подпружиненных точек крепления стола. Для вариантов с 2 стойками Z доступно либо 4, либо 6 точек. Для вариантов с 4 стойками доступно 4, 6, 8 и 9 точек
Количество стоек оси Z | 2 |  | Количество стоек и приводов оси Z зависит от габарита области печати, но по желанию может быть скорректировано. Рекомендуется: При Y меньше 300 мм: 2 стойки и 2 привода При Y от 300 до 400 мм: 4 стойки и 2 привода При Y больше 400 мм: 4 стойки и 4 привода
Количество приводов оси Z | 2
Электроника
Материнская плата | Fysetc spider |  | На данный момент Fysetc Spider — это единственная официально поддерживаемая плата. Это не значит, что надо брать именно её, принтер можно собирать и на других вариантах. Просто конфигов и схем подключения под другие платы в ближайшее время не будет.
Управляющая плата | Orange Pi Lite |  | Ввиду дороговизны плат Raspbeery Pi, для установки внутрь принтера предлагается выбирать платы Orange Pi. В качестве альтернативы может выступить любой компьютер с USB и linux.
Печатные детали
Плотность филамента для несущих деталей | 1,05 г/см³ |  | Характеристики филамента, который будет использоваться для печати нагруженных деталей механики принтера (каретки, детали печатающей головы и т. д.). Рекомендуется использовать прочный, жесткий, термостойкий и хорошо спекающийся материал. Например: PP GF; PP GF30; PA12 GF30; PA6 GF30 и подобные. Плотность указывается в г/см³, цена в $/кг.
Стоимость филамента для несущих деталей | $40,00 |  | Стоимость килограмма филамента, из которого будут печататься основные несущие детали принтера
Плотность филамента для вспомогательных деталей | 1,28 г/см³ |  | Характеристики филамента, который будет использоваться для печати вспомогательных деталей (петли, держатели катушек и т. д.). Рекомендуется прочный, дешевый и легкий в печати филамент с термостойкостью от 70 градусов. Идеальным выбором будет PETG, но возможна замена. Плотность указывается в г/см³, цена в $/кг.
Стоимость филамента для вспомогательный деталей | $14,00 |  | Стоимость килограмма филамента, из которого будут печататься основные несущие детали принтера
Константы
Курс доллара | 80,00 ₽
Вывод
Габарит принтера по X | 670 мм |  | Учтена толщина зашивки 4мм. Не учтена высота головок винтов и навесное оборудование (держатели катушек, ручки дверц и т. д.)
Габарит принтера по Y | 490 мм
Габарит принтера по Z | 430 мм
Цена | $1 034,55 | 82 764,06 ₽ | Не учтена цена проводки и зашивки
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

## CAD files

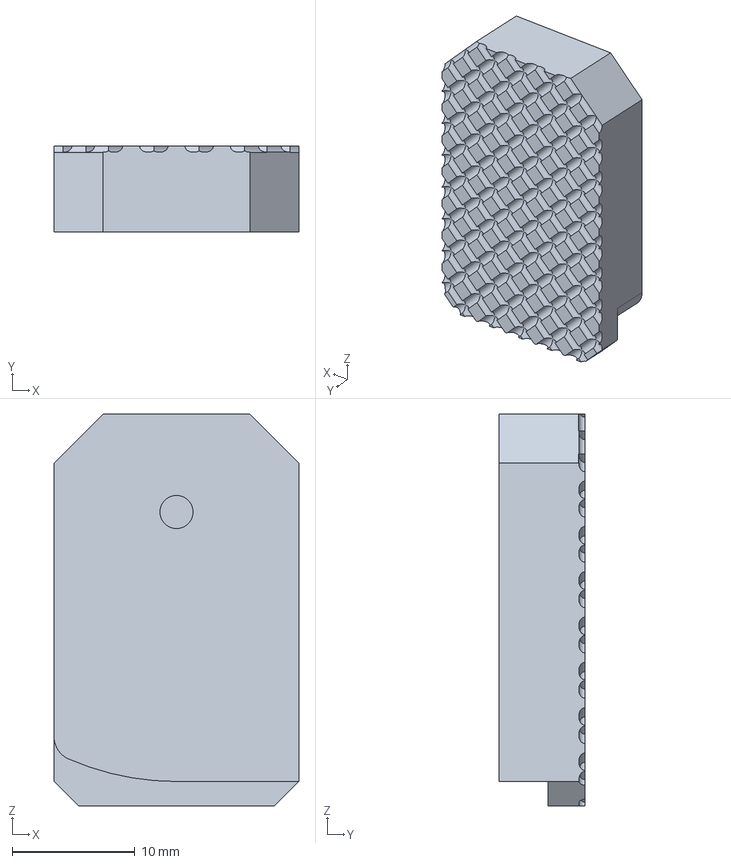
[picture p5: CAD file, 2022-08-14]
Parts/STEP/V07-04-10-01 - Back door lock.stp
20.0 x 7.00 x 32.0 mm

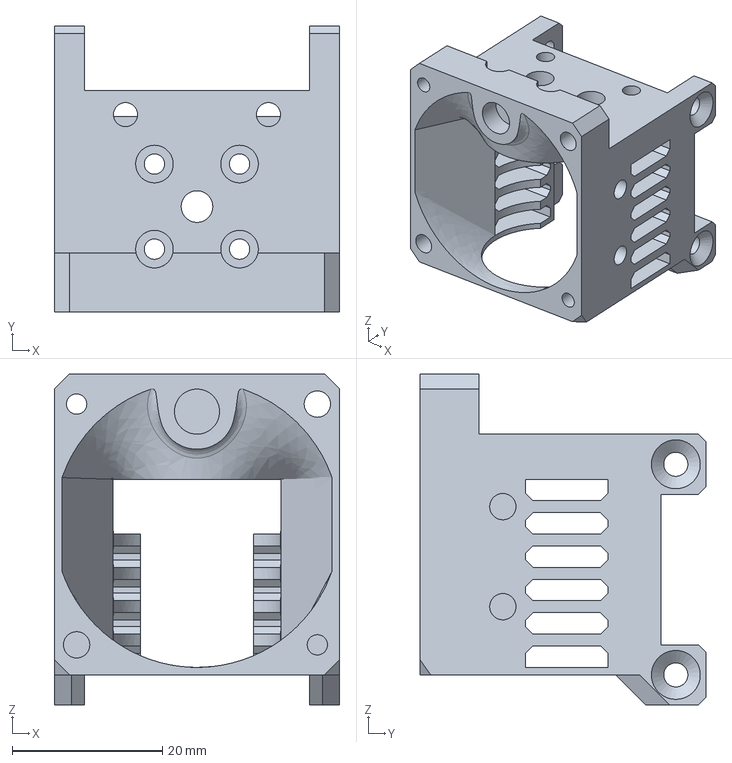
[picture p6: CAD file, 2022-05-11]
Parts/STEP/V07-01-01-04-02 - Lite print head case.stp
37.9 x 38.0 x 44.0 mm

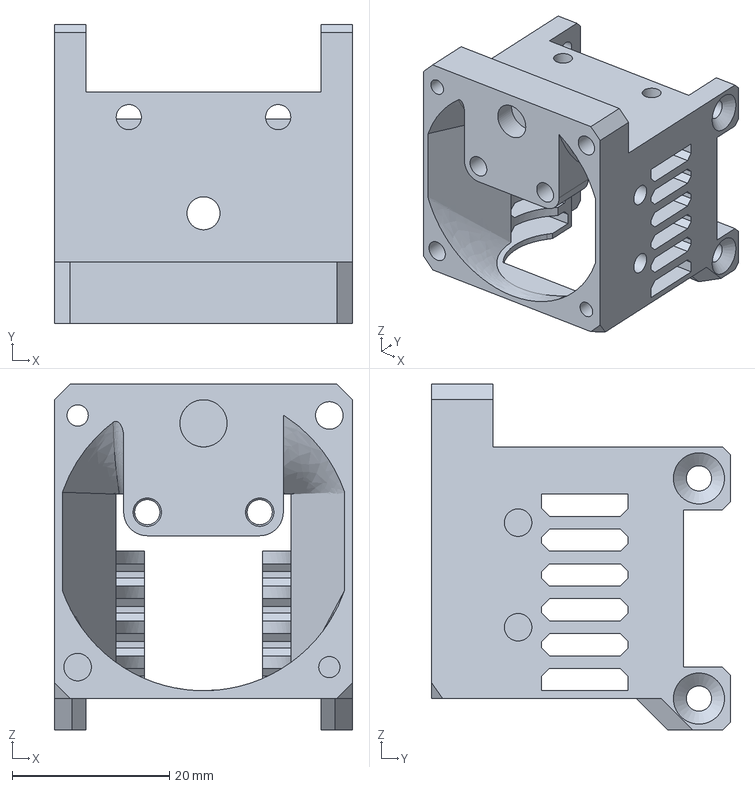
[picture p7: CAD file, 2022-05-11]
Parts/STEP/V07-01-01-04-06 - Lite print head case for CR10 heatsink.stp
37.9 x 38.0 x 44.0 mm

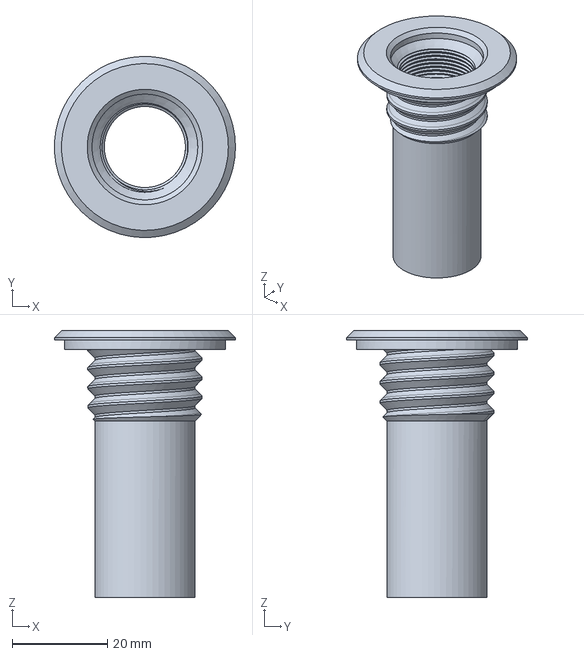
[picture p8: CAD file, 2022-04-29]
Parts/STEP/V07-04-11 - Print head cable guide.stp
38.0 x 38.0 x 56.0 mm

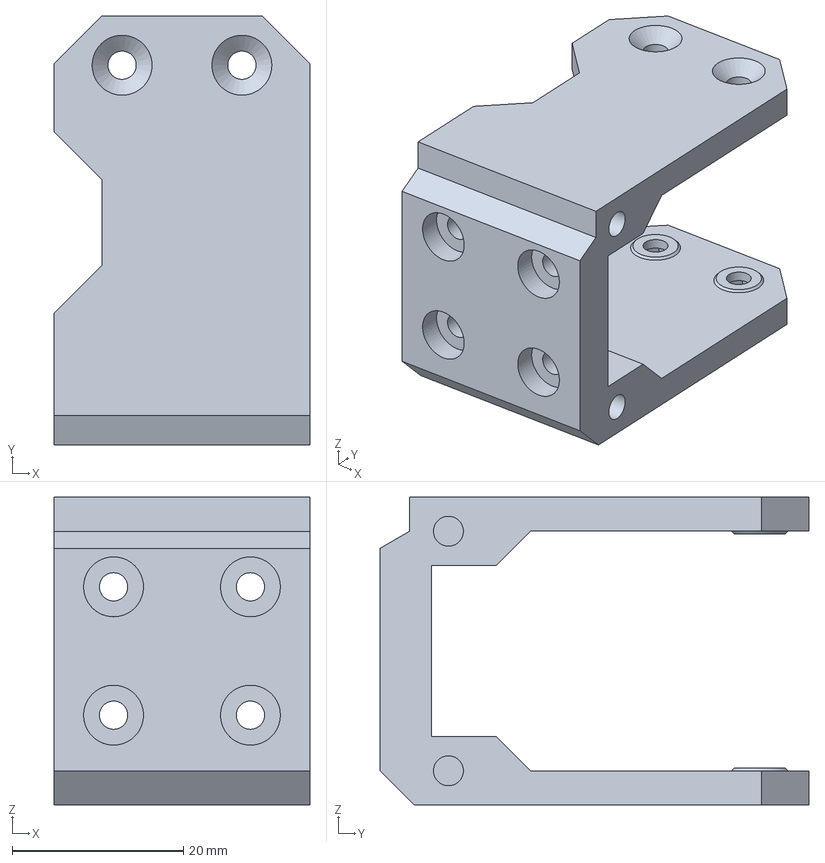
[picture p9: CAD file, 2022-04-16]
Parts/STEP/V07-01-01-04-01 - Lite print head mount.stp
29.9 x 50.1 x 36.0 mm

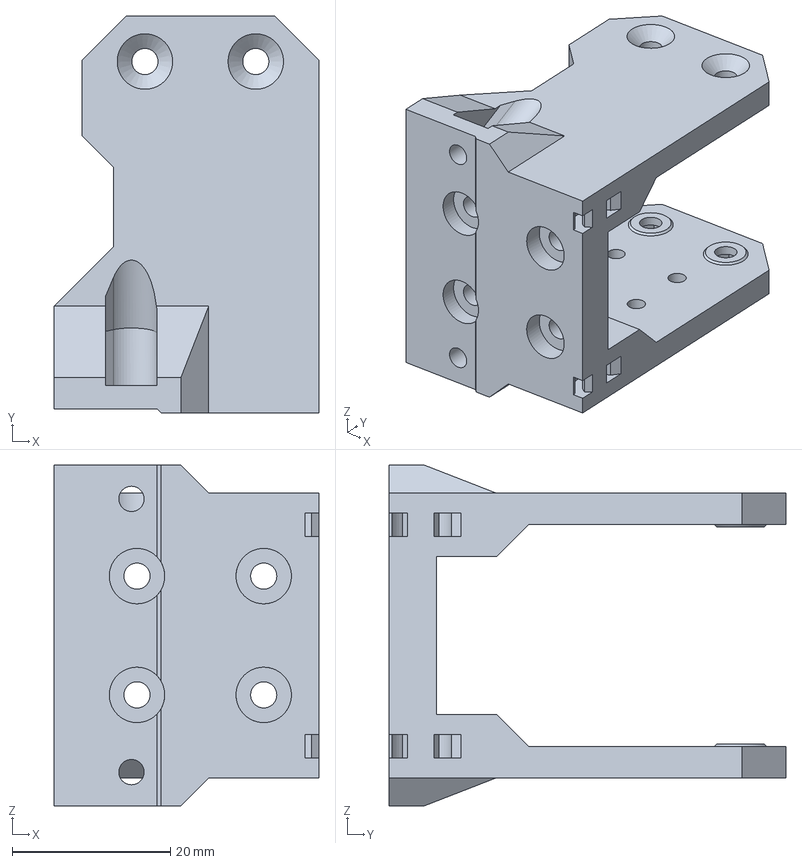
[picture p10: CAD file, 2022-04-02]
Parts/STEP/V07-01-01-03-01 - Matrix lite mount.stp
33.4 x 50.1 x 43.0 mm

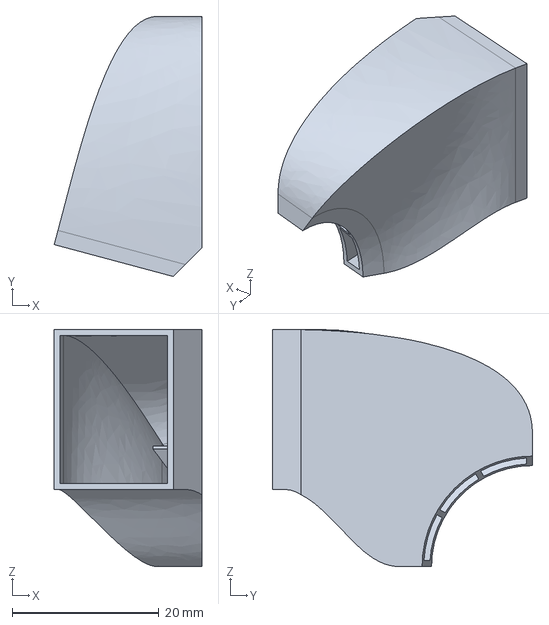
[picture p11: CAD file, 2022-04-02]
Parts/STEP/V07-01-01-03-04(L) - Matrix 5015 volcano back fan duct.stp
20.1 x 35.4 x 32.3 mm

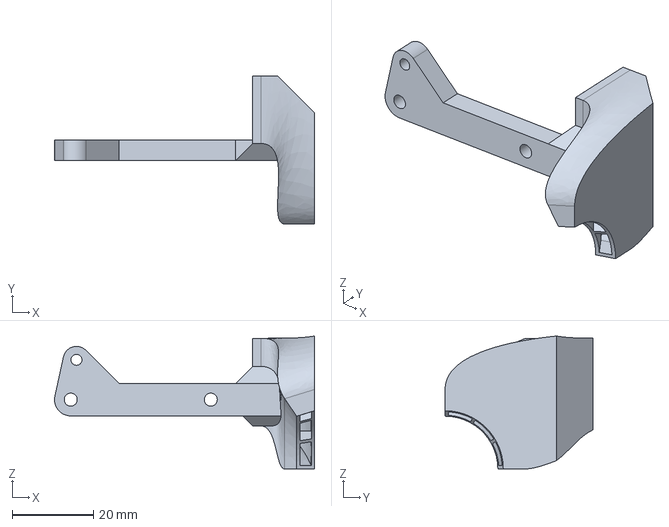
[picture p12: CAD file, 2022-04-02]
Parts/STEP/V07-01-01-03-02(L) - Matrix 5015 V6 fan duct.stp
64.0 x 36.4 x 32.8 mm

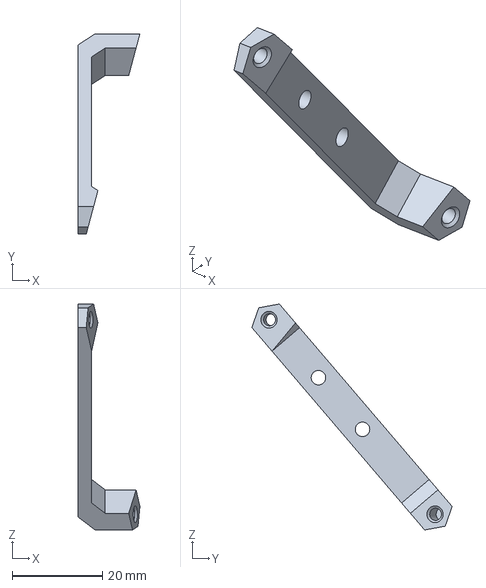
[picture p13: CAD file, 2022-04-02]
Parts/STEP/V07-01-01-03-05 - Matrix 5015 back fan mount.stp
13.7 x 44.3 x 50.0 mm

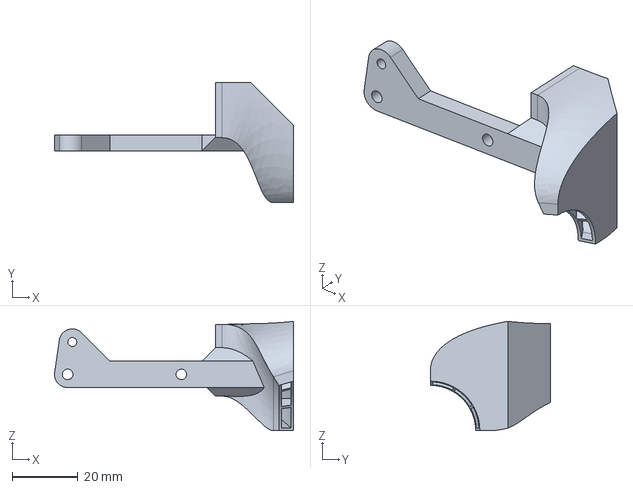
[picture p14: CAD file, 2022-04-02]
Parts/STEP/V07-01-01-03-03(L) - Matrix 5015 volcano front fan duct.stp
72.5 x 36.5 x 33.2 mm

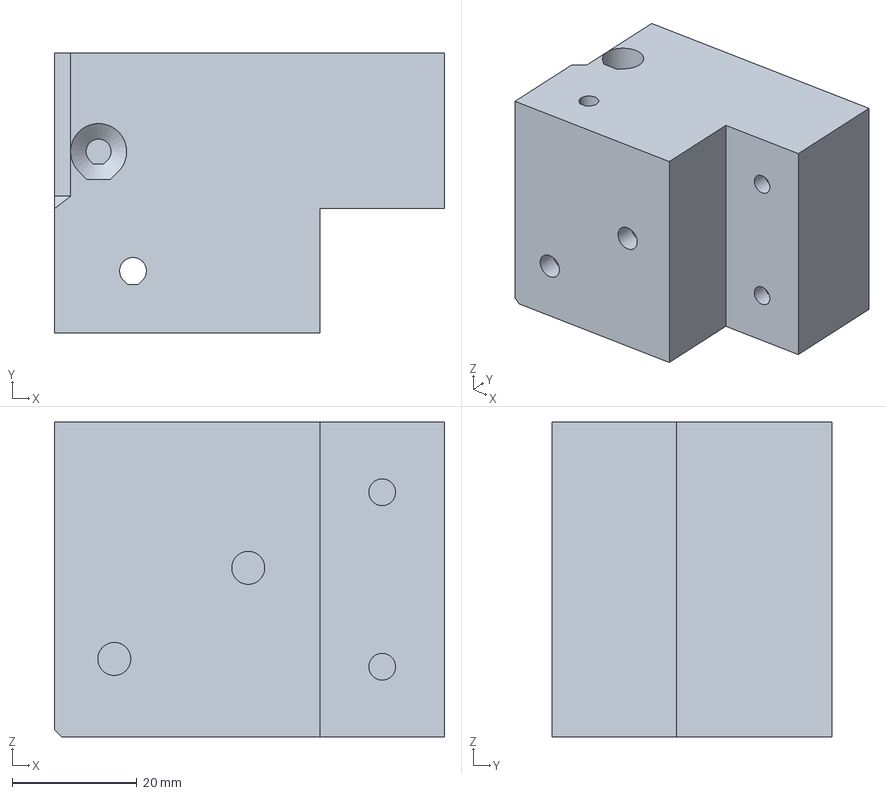
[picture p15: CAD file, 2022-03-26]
Parts/STEP/V07-01-05-01 - Right belt tensioner base.stp
62.6 x 45.0 x 50.5 mm

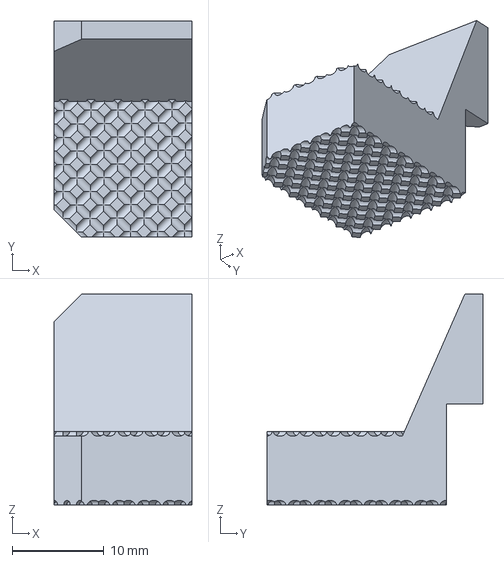
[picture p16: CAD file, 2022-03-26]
Parts/STEP/V07-04-07-03 - Front door handle.stp
15.0 x 23.6 x 23.0 mm

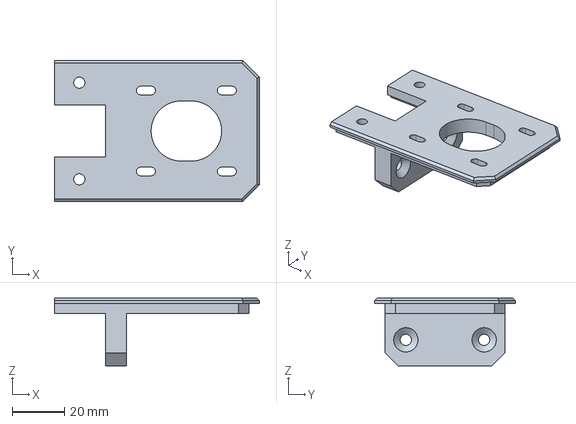
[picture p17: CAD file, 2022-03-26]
Parts/STEP/V07-03-02-01 - Z axis motor mount.stp
78.5 x 54.0 x 26.0 mm

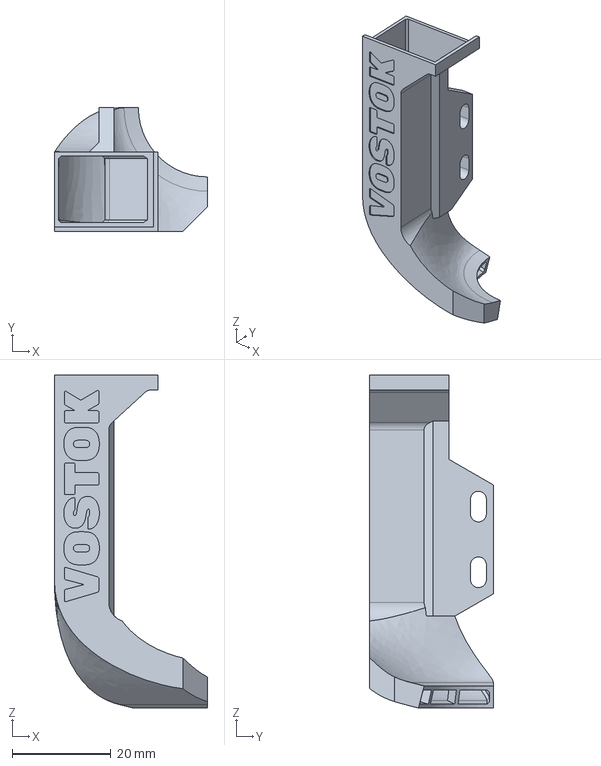
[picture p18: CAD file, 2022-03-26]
Parts/STEP/V07-01-01-04-05 - LPH V6 5015 front fan duct.stp
31.0 x 25.0 x 67.4 mm

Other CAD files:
Parts/STEP/V06-01-01-02-02(L) - BMG V6 5020 fan duct.stp
Parts/STEP/V07-01-06-01 - X axis mechanical endstop mount.stp
Parts/STEP/V05-03-03-01-01 - 2020 to 2060 mount.stp
Parts/STEP/V07-01-04-03-01 - Belt tensioner slider (0.5XY).stp
Parts/STEP/V05-01-01-01-03 - X axis stopper.stp
Parts/STEP/V05-01-04-02-01 - Belt tensioner slider.stp
Parts/STEP/V05-03-03-01-02 - Bed arm end.stp
Parts/STEP/V05-07-01 - Enclosure top corner.stp
Parts/STEP/V05-07-05 - Enclosure top panel corner.stp
Parts/STEP/V05-07-06-01 - Enclosure top hinge part A.stp
Parts/STEP/V05-07-06-02 - Enclosure top hinge part B.stp
Parts/STEP/V06-03-03-01-04 - 2020 to 2020 mount.stp
Parts/STEP/V07-01-01-01-01 - Y axis carriage base.stp
Parts/STEP/V07-01-01-01-02 - Y axis belt clamp.stp
Parts/STEP/V07-01-01-01-04 - Roller spacer.stp
Parts/STEP/V07-01-01-02-01 - BMG mount.stp
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

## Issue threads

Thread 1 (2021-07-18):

В BOM в списке покупок не отмечено твердотельное реле при выборе АС стола отличного от AC 400х250

MIOB, 2021-07-18:
В табличке на листе "покупные изделия" твердотельное реле отмечается только если выбран стол AC 400х250. Насколько я понимаю реле нужно при выборе любого АС стола.

dmitry-sorkin, 2021-07-18:
Исправил в [https://github.com/dmitry-sorkin/K3D-VOSTOK/commit/b359f4ea0b25733abac577b17e023347205ff314](этом коммите)

Closed 2021-07-18.

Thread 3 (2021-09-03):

Console bottom mount of side walls

r8d8, 2021-09-03:
Planning to build printer, and noticed that side walls has console unsupported "tail", where bottom 20x20 mm base profile lies (see attachments). This is pretty fragile part, as in case one will try to lift printer from side and potentially can crack side walls. Besides, edge is to sharp, to hold it in hand with heavy load of printer
My proposal is to use 60x20mm profile, same as on top of printer, this will allow to extend wall support all the way down. Also it will give flat rigid surface to hold printer from sides. It shouldn't add too much cost  into BOM, and you don't need rebuild mechanics, just extend legs (currently there is 50mm offset, see Fig.1)

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

dmitry-sorkin, 2021-09-03:
It isn't unsupported. There is blind joint in the end of each profile. I will add blind joints to assembly later, when whole frame will be tested.

r8d8, 2021-09-03:
Got it, thanks.

Closed 2021-09-03.

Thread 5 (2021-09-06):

Проблема с крепежом V05-01-01-02-03 - Belt mount

Foxcor, 2021-09-06:
По стандарту DIN 7991 или DIN 965 длина винта идет 16 потом 20 мм. Так вот, 16 мм мало, 20 мм много, упирается в ремень.
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

dmitry-sorkin, 2021-09-28:
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
Пока решать вот так. До переделки головы изменять эти детали не буду.

dmitry-sorkin, 2022-03-26:
Не актуально ввиду временного прекращения поддержки кинематики markforged

Closed 2022-03-26.

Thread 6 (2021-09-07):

Not all product items are definitely on AliExpress (Не все позиции однозначно определяются по ссылке на AliExpress)

petrovi4, 2021-09-07:
Русское описание ниже
-----------------
Some links in the BOM to products are described in too general terms.
Sellers on AliExpress can edit the product, add options that are not compatible with the printer. For example, position 13 in the BOM is called "Fan 5020", and the link leads to a product that has 3 voltage options: 5, 12 and 24 volts. This causes additional confusion and increases the likelihood of an error, although this is easily avoided if we write a full description of the product in the BOM in the name of the product or in the description.

For example, in position 13, we can add the description "50x20, 24V Centrifugal turbine fan". It will also help to detect and restore dead links to lots that are no longer relevant and are not for sale.

---

Некоторые ссылки в BOM на товары описаны слишком общими терминами.
Продавцы на AliExpress могут отредактировать товар, добавить опции, которые не совместимы с принтером. Например, позиция 13 в BOM называется "Вентилятор 5020", а ссылка ведет на товар, в котором есть 3 варианта вольтажа: 5, 12 и 24 вольта. Это вызывает дополнительную путаницу и повышает вероятность ошибки, хотя этого легко избежать если в BOM в названии товара или в описании мы напишем полную характеристику товара.

Например, для позиции 13 мы можем добавить описание "Центробежный турбинный вентилятор 50x20, 24V" что хотя и не однозначно описывает товар (нет бренда, это ничего не говорит о качестве товара), зато указывает на значимые характеристики позиции. Это так же поможет обнаруживать и восстанавливать мертвые ссылки на лоты, которые уже не актуальны и не продаются.

petrovi4, 2021-09-07:
С удовольствием возьму на себя всю рутину и формально конкретизирую каждую позицию, если Дмитрий в комментарии укажет какие значение для критических характеристик каждой позиции следует использовать. Тот же вентилятор для хотенда я как-то по-умолчанию думал что должен быть 24-х вольтовым, а ссылка на "Вентилятор 30х30х10" (позиция 12) ведет на 12-ти вольтовую версию.

dmitry-sorkin, 2021-09-07:
Нет необходимости в какой-то конкретизации. Все ссылки даны для примера, в названии позиции указывается вся необходимая информация для его покупки. Если что-то не уточнено, значит это не важно. В случае примера с вентиляторами: рекомендуемые платы имеют выбор напряжения на питание вентиляторов, поэтому не указано какие конкретно брать, это оставляется на усмотрение пользователей.

petrovi4, 2021-09-08:
Это авторский проект, и, возможно, я тут со своими комментариями как корова в посудной лавке, поэтому заранее прошу прощения :)
Но раз уж проект открытый, то позвольте предложить всё таки существенные для сборки характеристики указывать в BOM'е

Мой айтишный опыт подсказывает что даже если в случае с тем же вентилятором мы выбирая лот на Али увидели, что продаются варианты 5, 12 или 24 вольта, у нас плата, которая поддерживает выбор напряжения 5, 12 или 24 вольта, то вместо "Вентилятор 5020" все таки лучше будет написать "Вентилятор 5020 - вольтаж любой из следующих: 5/12/24".
Это не сложно, но любого будущего сборщика не ставит в тупик наличие трёх вольтажей на странице лота.
Завтра продавец может добавить четвертый вольтаж, который уже не будет поддерживаться какой-то из плат. И купленный кулер может быть уже не совместим.
Если что-то может пойти не так - это обязательно случится.
Если пользователь (в данном случае человек, который собирает Восток) может купить что-то не то, или собрать как-то не так - он обязательно это сделает.  Зачем давать такую возможность, если избежать этого так легко?

zmeygeruch, 2021-09-18:
> Мой айтишный опыт подсказывает что даже если в случае с тем же вентилятором мы выбирая лот на Али увидели, что продаются варианты 5, 12 или 24 вольта, у нас плата, которая поддерживает выбор напряжения 5, 12 или 24 вольта

Сами по себе 3D принтеры - чисто инженерское устройство. Не для домохозяек. А тут еще и самосбор в альфа версии. Айтишный опыт обычно складывается из отношения юзеров к вашему готовому продукту :) А тут будут собирать люди, которым хотя бы немного понимают в чертежах, схемах, электронике. Достаточно, что там будет вентилятор 5020. Да и, как Дмитрий выше неписал, напряжение у всех может быть разное, а внесение в описание 5/12/24V совершенно никак не сужает круг поиска. :)

petrovi4, 2021-09-18:
>> Сами по себе 3D принтеры - чисто инженерское устройство. Не для домохозяек.
Почему? Что плохого если 3d принтер будет доступен и для условных домохозяек? Мне кажется, вариант "лучше минимум документации, чтобы только истинные инженеры могли в 3d печать" это огораживание информации, не идущее любой отрасли в плюс. От популяризации, в подавляющем большинстве случаев, выигрывают все.
Я, признаться, не очень хочу обосновать почему "больше документации" лучше чем "меньше документации" (без каких-то предельных, конечно, случаев). Поэтому, так как это всё ещё по духу и по сути - авторский проект, а значит автору единолично принимать решение.
Ещё раз прошу прощения, если моя точка зрения показалась автору навязыванием. Благо, я успел ещё и в чате "поныть" )

dmitry-sorkin, 2021-09-28:
Доработаю документацию, но после исправления важных косяков

dmitry-sorkin, 2021-09-28:
Решено в d32101765807e79c6c126dd09d6f5ab5794d603f

Closed 2021-09-28.

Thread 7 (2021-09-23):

Incorrect number of 623 bearings in BOM 0.5.6-alfa / Не верное количество 623 подшипников в BOM 0.5.6-alfa

Suhanovd, 2021-09-23:
Количество подшипников 623zz и f623zz d BOM 8 и 16 соответственно. А на самом деле должно быть 10 и 20, так мест с их установкой 10.
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

dmitry-sorkin, 2021-09-28:
Решено в d32101765807e79c6c126dd09d6f5ab5794d603f

Closed 2021-09-28.

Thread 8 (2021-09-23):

Шкивы в BOM

DeltaDesignRus, 2021-09-23:
В BOM в примере, какие шкивы нужно покупать, ссылка на поштучный товар, а он дороже.
Лучше заменить на товар, где в комплекте сразу 3 штуки, дешевле на треть почти, за такие же шкивы.
https://aliexpress.ru/item/32650791423.html

dmitry-sorkin, 2021-09-28:
В разных комплектациях нужно разное количество шкивов. Поэтому указывать на готовые наборы с определенным количеством некорректно КМК. Позже, если буду делать альтернативные для товаров ссылки, добавлю наборы в альтернативы.

Closed 2022-03-26.

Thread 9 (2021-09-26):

Восстановленные вентиляторы 3010 в BOM

DeltaDesignRus, 2021-09-26:
Ссылка на вентиляторы обдува радиаторов экструдеров ведет на восстановленные (БУ) вентиляторы низкого качества.

dmitry-sorkin, 2021-09-28:
Решено в d32101765807e79c6c126dd09d6f5ab5794d603f

Closed 2021-09-28.

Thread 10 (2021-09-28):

Ошибка в модели kls1-as-303-1-2.

Foxcor, 2021-09-28:
В модели kls1-as-303-1-2 не хватает частей, на модель самого принтера не влияет, но не красиво)))
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

https://grabcad.com/library/kls1-as-303-1-2

dmitry-sorkin, 2021-09-28:
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

У меня всё норм. Возможно, проблема при экспорте/импорте возникла

Closed 2021-09-28.

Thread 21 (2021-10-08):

BOM. Количество пружин и Bed arm'ов

Kest430, 2021-10-08:
вопрос по количеству Bed arm'ов

Я планирую делать стол 400*400.

В бом на листе Печатные детали есть позиция "V05-03-03-01-02 Bed arm". В столбце "Количество" посчиталось, что надо 8. Но в комментах к этой позиции написано:
"Если 4, то 2 обычных и 2 отражённых
Если 6, то 4 обычных и 2 отражённых
Если 9, то 6 обычных и 3 отражённых"

я так понимаю, что это ошибка и должно быть "Если 8, то 6 обычных и 2 отражённых"

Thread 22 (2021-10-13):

Добавить в BOM розетку

bass89, 2021-10-13:
В BOMe нет входной силовой розетки, а в проекте то она есть)
вроде как вот эта AC-08
https://aliexpress.ru/item/4000469723664.html?item_id=4000469723664&sku_id=10000001888865430

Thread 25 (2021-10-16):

Исправление формулы установки цены профиля

StasBronchukov, 2021-10-16:
На листе **"Профиль алюминиевый"** в ячейках столбца **E "Цена профиля [$/м]"** некорректная запись формулы, которая не вызывает ошибки при открытии **LibreOffise**, но вызывает ошибку при открытии в **Google таблицы**. Ошибка вызвана тем что в **Google таблицы** в функции ЕСЛИМН каждому значению должно соответствовать логическое выражение - в исходной формуле в самом конце значению  **"3,12"** не соответствует никакое логическое выражение.

**Исходная формула**
=ЕСЛИМН(B2="2020 T-slot";4,58;B2="2040 T-slot";7,91;B2="2060 T-slot";11,86;B2="2020 V-slot";4,49;B2="2040 V-slot";7,81;B2="2060 V-slot";11,47;B2="2020 T-slot облегчённый";231/74;3,12)

**Предлагаемая исправленная формула**
=ЕСЛИМН(B2="2020 T-slot";4,58;B2="2040 T-slot";7,91;B2="2060 T-slot";11,86;B2="2020 V-slot";4,49;B2="2040 V-slot";7,81;B2="2060 V-slot";11,47;B2="2020 T-slot облегчённый";231/74)

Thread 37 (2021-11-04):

Количество печатный деталей V06-01-03-02 в BOM.v0.6.4-alpha

Kest430, 2021-11-04:
Печатная деталь **V06-01-03-02**

В BOM.v0.6.1-alpha было _прописано_, что их должно быть 2 штуки и в комментах написано _"Половина обычные, половина отражённые"_

в BOM.v0.6.4-alpha их количество считается по какой-то формуле и для кинематики 0,5ХУ БОМ выдает, что их надо только 1 штуку. Тем не менее в сборочном STEP-файле их изображено 2 штуки - одна обычная, вторая - зеркальная

Closed 2021-11-15.

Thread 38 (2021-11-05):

Примечания к покупным изделиям в БОМ

Kest430, 2021-11-05:
в БОМ на листе Покупные изделия есть несколько позиций, ссылки на которые ведут на лоты, где есть выбор необходимого товара/размера/типа. Но не указано, какой именно товар/размер/тип нужно заказать.

Чтобы было меньше вопросов желательно указать примечания.

- **Винт Tr8x2**. Не указано какой нужен шаг резьбы. В чате об этом были вопросы.
- **Гайка POM Tr8x2**. Не указано какой нужен шаг резьбы
- **Концевик механический**. В чате на мой вопрос вы написали, что надо с закругленной на конце лапкой (Arc Lever)

dmitry-sorkin, 2021-11-15:
У винта и гайки указана резьба Tr8x2 - это однозаходная трапецеидальная резьба с шагом и ходом 2мм. Четырёхзаходная резьба обозначается Tr8x8 (P2).
Касательно концевика - укажем тип

Closed 2021-11-15.

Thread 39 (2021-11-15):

Баги держателей катушек

DeltaDesignRus, 2021-11-15:
1. В детали V05-06-01-01-02 - Inner spool holder rocker plate v1 уступ не позволяет повернуть эту деталь на такой угол, который позволяет деталь V05-06-01-02 - Inner spool holder mount part A v6
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
2. В детали V05-06-01-02 - Inner spool holder mount part A v6(Mirror) нужно убрать пазы под гайки, потому что туда удобнее вставлять винты, которые притянутся к профилю через пазовые гайки.
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
3. Подшипники имеют свободный ход, отчего собранный держатель жидковат.
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
4. Крепление роликов к подшипникам сейчас на трении, либо придется клеить подшипники. Как вариант сделать, как я (модель в чате кидал)
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
5. Ролики можно сделать не цилиндрическими, а в виде бочонков (с радиусом). Должно дополнительно помочь центрировать катушки.

Dimyc, 2021-12-14:
Поддерживаю предложения DeltaDesignRus. Нужны какие-то фиксации подшипников, т. к. в данной конструкции при прослаблении размеров держатель разваливается. По п.5 еще хочу добавить, что в ролике желательно добавить упор для подшипника, т. к. если диаметр внутреннего отверстия будет больше диаметра внешней обоймы подшипника, последний соскальзывает с оси опоры и проваливается внутрь отверстия ролика.

Dimyc, 2021-12-14:
А, уже заметил, что подшипники фиксируются маленькими винтиками. Теперь мысль Соркина понятна. :)

Dimyc, 2021-12-26:
Погонял я этот держатель и пришел к выводу, что его конструкция не очень хороша для использования типа - отпечатал, собрал и пользуешься. Почему? Не все принтеры настроены для печати с идеальными размерами. Поэтому при сборке будет тяжело добиться соосности установки роликов, т. к. при таких размерах подшипников и при прослаблении размеров не получится установить подшипники без дополнительной фиксации. Это приведет к тому, что либо вся конструкция будет разваливаться при вращении катушки (будут выпадать подшипники из посадочных мест), либо ролики будут крутиться туго или с заеданием. Далее - у большинства будет явно выраженный шов при печати роликов. В совокупности с тугим вращение роликов, прокрутить катушку будет затруднительно. Она будет проскальзывать на шву. При определенном натяжении прутка, не знаю как на CoreXY, но на дрыгостолах еще и голова может немного приподняться. В результате чего появятся вот такие щели на модели (см. фото). Особенно это будет происходить на тяжелых катушках, т.к. пруток уходит вниз и при натяжении он еще сильнее будет зажимать катушку между роликами. Раньше у меня часто были подобные проблемы + слои выкладывались не равномерно. После того как повесил катушку на вал с подшипниками, проблема ушла. Правда появилась новая - приходилось немного подтормаживать катушки, т.к. иногда она по инерции свободно прокручивалась на несколько оборотов. Особенно когда ставил новую катушку. :)

Мне кажется, нужно как-то переделывать держатели под осевое крепления катушки с использование подшипников, например, 608ZZ 8x22x7mm. Rfr 'nj cltkfnm e vtyz gjrf bltq ytn :)

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

Closed 2022-03-26.

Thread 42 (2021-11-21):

Изменение узла крепления мотора Y

izlat, 2021-11-21:
Предлагается рассмотреть возможность переделки крепления мотора Y, для возможности установки двигателей других размеров, например, для установки 17HS4401 (37.5мм).

Closed 2022-03-26.

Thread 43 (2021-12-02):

Количество продольных балок рамы стола

Laker87, 2021-12-02:
В файле BOM количество продольных балок рамы стола не меняется в зависимости от количества точек крепления стола и всегда равно 3.

dmitry-sorkin, 2022-03-26:
Исправлено в версии 0.7

Closed 2022-03-26.

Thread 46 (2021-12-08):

Не правильно считается количество шайб М3

The-Futur1st, 2021-12-08:
Каждый Roller Assembly содержит 2 шайбы
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
В бом же считается что 4
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
Итого показывает что шайб нужно в 2 раза больше.

dms78, 2021-12-14:
Вообще нужно даже больше,  так как пространство между двумя средними шайбами забивается тоже шайбами(кто-то печатает проставки)

dmitry-sorkin, 2022-03-26:
Не актуально так как в версии 0.7 сборки роликов изменены

Closed 2022-03-26.

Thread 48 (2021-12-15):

Отсутствие припуска по Y уменьшает рабочую длину по Y почти на 5 см.

matuzyaka, 2021-12-15:
Проверяю то что выдает Бом. Получается что при столе 200 по у надо 6020 профиль длиной 350мм. При такой длине для движения головы и каретки у остаётся только 278 мм от профиля до профиля. Длина от дальнего края каретки у до противоположной плоскости головы 114мм. То есть при рекомендованной Бом длине 2060 350мм я получу только 164мм по у вместо 200 и то не факт. Получается, что не выставляя "припуск по у" в настройках Бом теряется почти 5 см рабочей плоскости.

Closed 2022-03-26.

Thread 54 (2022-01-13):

V05-01-01-02-03 X axis belt mount предлагается печатать 2шт  для кинематики 0.5XY

izlat, 2022-01-13:
При выборе в BOM кинематики 0.5XY деталь для CoreXY - V05-01-01-02-03 - X axis belt mount, предлагается напечатать 2 шт, должно быть 0 шт.

dmitry-sorkin, 2022-03-26:
Исправлено в версии 0.7

Closed 2022-03-26.

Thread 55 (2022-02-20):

Ошибка в формуле в `K3D-VOSTOK/Docs/BOM v0.6.5-alpha.ods`

TEH30P, 2022-02-20:
`BOM v0.6.5-alpha.ods` по адресу `$'Покупные изделия'.C58` битая ссылка в формуле:

`=IFERROR(IFS(#REF!=#REF!,0,#REF!=#REF!,0),1)`

---
И ещё, это конечно не ошибка, и вы, как автор, имеете право меня игнорировать. Но по-моему лучше не делать пробелы в именах файлов, то там то сям это создаёт проблемы. Может лучше перименовать файл в `BOM-v0.6.5-alpha.ods`

TEH30P, 2022-02-22:
И ещё `$'Покупные изделия'.D29=($Расчёты.B17+50)/1000` тут, по-моему должно быть `$'Покупные изделия'.D29=$Расчёты.B19`. Т.к. +50 это припуск, который настраивается, а не всегда есть. Вообще ячейки `$Расчёты.B16` и `$Расчёты.B17` лишние, в формулах они всё время на 1000 деляться, т.е. повторяют `$Расчёты.B18` и `$Расчёты.B19`.

dmitry-sorkin, 2022-03-26:
Неактуально ввиду полной переработки BOM в версии 0.7

Closed 2022-03-26.

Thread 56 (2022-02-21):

Исправить мелкие баги 0.7 версии

DeltaDesignRus, 2022-02-21:
В "V07-01-03-01 - Y shaft end holder" задний винт очень трудно крутить, когда мотор уже установлен.
В "V07-01-02-01 - X axis motor mount" для шкива вверху не хватает места, надо добавить пространство глубиной в 1мм, и на 1мм больше диаметром, чем сам шкив.
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
В "V07-01-02-01 - X axis motor mount" есть отверстие, куда не влезает головка винта с полукруглой головкой. Отверстие нужно увеличить в модели. Я напечатал как есть, и винт туда не вошел (мостик провис), пришлось страдать, что бы рассверлить отверстие. Если начать сверлить просто так, то сверло моментально зацепится за дно отверстия и пробьет деталь насквозь.
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
В "V07-01-03-01 - Y shaft end holder" между юбкой шкива и козырьком (на котором лежит кабель) зазор недостаточный, что бы туда можно было завести ремень сбоку.
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
В "V07-01-03-02 - Y axis motor mount v02" Нужно увеличить вырезы под ключ.
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
Так же в этой детали нужно увеличить на 2мм диаметр отверстия, куда входит хвостовик шкива кольцевого ремня, который на валу. Ещё в этой детали мотор расположен так, что кольцевой ремень даже без натяжителя уже хорошо натянут. Надо на 1мм поднять мотор вверх.
Нужно перевернуть корпус натяжителя, и разместить ролик натяжителя снаружи кольцевого ремня.
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
В сборке "V07-01-01-01-00(L) - Y axis carriage" есть 2 проблемы. "V05-01-01-01-02 - Y axis belt clamp" имеет высоту 9мм, что избыточно, хватит и 8мм. Ремень, при движении балки по Y иногда резонирует и стучит по этой детали. Эти резонансы на ремне можно убрать, добавив под ремень ролики успокоители, но зазор между ремнем и этой деталью такой, что успокоители поставить будет невозможно, а вот если уменьшить высоту, то всё влезет.
У "V07-01-01-01-01 - Y axis carriage base" часть, к которой притягивается ремень, имеет толщину 4мм (либо 5мм, если измерять по бортику), и у меня её снова погнуло! Надо сделать её тоже 8мм, и проблема исчезнет.
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

Closed 2022-03-26.

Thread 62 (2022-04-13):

Два разных экструдера в step

Holyfriend, 2022-04-13:
Я не знаю, это фишка, или баг.

В степ v0.7.1 от 02.04.2022 два разных экструдера, наложены друг на друга.

dmitry-sorkin, 2022-04-16:
Это не баг. В сборке все вариации поставляются включенными. Вы можете скрыть ненужные.

Closed 2022-04-16.

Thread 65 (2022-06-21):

Программы для просмотра сборки

wirebeard, 2022-06-21:
Какими бесплатными программами можно просматривать файлы stp и x_t со сборкой принтера? Возможно добавить сборку в формате a3d для просмотра программой КОМПАС-3D Viewer?

dmitry-sorkin, 2022-08-11:
В компасе можно открывать и step, и pasasolid

Closed 2022-08-11.

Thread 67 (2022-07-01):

Ошибка при расчёте зашивки при выборе варианта с 4 стойками и 2 моторами Z

ralex2304, 2022-07-01:
При выборе варианта с 4 стойками и двумя моторами расстояние между стойками z меньше на 20 мм, чем должно быть. Ориентируюсь по сборке Дмитрия и данным из BOM по продольной балке стола. То есть 2 варианта, либо раздвинуть стойки z на 20 мм, либо продольную балку стола укоротить на 20 мм. Прилагаю dxf и данные из BOM
BOM 0.7.3
DXF Generator v0.7.2b
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
[Result.zip](https://github.com/dmitry-sorkin/K3D-VOSTOK/files/9030938/Result.zip)

Closed 2022-08-03.

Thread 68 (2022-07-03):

Ошибка при печати некоторых деталей

DoFomin, 2022-07-03:
V07-04-11 - Print head cable guide
V07-04-12 - Print head cable guide nut
 Необходимо добавить оффсет (эквидистанту внутрь) так как не закручивается гайка

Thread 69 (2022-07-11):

Несколько замечаний по сборке.

DenDen1525, 2022-07-11:
Версия 7.3
1) BOM файл.
V07-01-03-01 - комментарий "Не зеркалится", а надо зеркалить половину.

2) Сборочный чертеж
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
По чертежу m3x8 полусфера.
По BOM таких винтов нет, есть потай и цилиндр
По факут лучше подходять m3x12

3) Сборочный чертеж
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
По чертежу m4x10 полусфера.
По BOM таких винтов нет
Подходят m4x12

4) Модели.
Не знаю как у всех, но у меня вот эта деталь
V07-01-07-01 - Y axis mechanical endstop mount.stl
не закрепляется нормально в профиле -слишком глубоко входить , и ту часть, что соприкасается с т-гайкой пришлось сточить на пол миллиметра.

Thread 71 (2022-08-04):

Добавить в BOM большущее предупреждение, что размер области XY != размеру плиты стола

FurrySphere, 2022-08-04:
В чате несколько человек уже писали, что накололись и купили плиты стола в размер области печати, в итоге плита меньше, чем нужно по Y на 50мм. Предлагаю прямо рядом с полем ввода области печати в BOM добавить три жирных красных свистка, вопящих о том, что плита стола нужна будет на 50мм больше по Y, чем область печати.

E1-G, 2022-08-08:
Оно там и так есть, просто люди не читают
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
)

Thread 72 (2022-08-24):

Ошибки в моделях 07-01-05-01 и 07-03-01-01

ralex2304, 2022-08-24:
В модели 07-01-05-01 слишком маленькое отверстия для винта, крепящего ремень

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

Увеличил диаметр, его взял из левого кронштейна

В модели 07-03-01-01 винты крепления детали к каретке openbuilds упираются в заднюю стенку

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

Добавил углубления

Исправленные файлы прилагаю
[STEP.zip](https://github.com/dmitry-sorkin/K3D-VOSTOK/files/9417266/STEP.zip)

Closed 2025-01-28.

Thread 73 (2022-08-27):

Ошибки в BOM

E1-G, 2022-08-27:
Неверно указано колличество спейсеров, на всю сборку принтера должно быть 8шт
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

Для полной сборки детали V07-01-01-01-01 необходимо 5 гаек м3 и 3 винта м3х35
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

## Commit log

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2021-07-18 Update BOM v0.5.2-alpha.ods
    Fixed wrong spring number error
    [BOM v0.5.2-alpha.ods]
2021-07-18 Update BOM v0.5.2-alpha.ods
    Fixed incorrect SSR count
    [BOM v0.5.2-alpha.ods]
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2021-07-20 Rename V05-03-01 - Z axis beam mount v9.step to V05-03-01-01 - Z axis beam mount v9.step
    [V05-03-01-01 - Z axis beam mount v9.step]
2021-07-20 Rename V05-03-02 - Z axis motor mount v2.step to V05-03-02-01 - Z axis motor mount v2.step
    [V05-03-02-01 - Z axis motor mount v2.step]
2021-07-20 Rename V05-03-03 - Heated bed 250x400 v2.step to V05-03-04-01 - Heated bed 250x400 v2.step
    [V05-03-04-01 - Heated bed 250x400 v2.step]
2021-07-20 Rename V05-03-04 - Bed arm v5.step to V05-03-03-01-02 - Bed arm v5.step
    [V05-03-03-01-02 - Bed arm v5.step]
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2021-07-20 Rename V05-03-06 - 2020 to 2060 mount v3.step to V05-03-03-01-01 - 2020 to 2060 mount v3.step
    [V05-03-03-01-01 - 2020 to 2060 mount v3.step]
2021-07-20 Rename V05-03-07 - optical endstop trigger v5.step to V05-03-05-02 - optical endstop trigger v5.step
    [V05-03-05-02 - optical endstop trigger v5.step]
2021-07-20 Rename V05-03-08 - Optical endstop mount v5.step to V05-03-05-01 - Optical endstop mount v5.step
    [V05-03-05-01 - Optical endstop mount v5.step]
2021-07-20 Rename V05-01-01-01-01 - Y axis carriage base v2.step to V05-01-01-01-01 - Y axis carriage base.step
    [V05-01-01-01-01 - Y axis carriage base.step]
2021-07-20 Rename V05-01-01-01-02 - Y axis belt clamp v1.step to V05-01-01-01-02 - Y axis belt clamp.step
    [V05-01-01-01-02 - Y axis belt clamp.step]
2021-07-20 Rename V05-01-01-01-03 - X axis stopper v2.step to V05-01-01-01-03 - X axis stopper.step
    [V05-01-01-01-03 - X axis stopper.step]
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2021-07-20 Rename V05-01-01-02-02(L) - BMG e3d v6 5020 fan duct v4.step to V05-01-01-02-02(L) - BMG e3d v6 5020 fan duct.step
    [V05-01-01-02-02(L) - BMG e3d v6 5020 fan duct.step]
2021-07-20 Rename V05-01-01-02-02(R) - BMG e3d v6 5020 fan duct v3.step to V05-01-01-02-02(R) - BMG e3d v6 5020 fan duct.step
    [V05-01-01-02-02(R) - BMG e3d v6 5020 fan duct.step]
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2021-07-20 Rename V05-01-02-01 - X axis motor mount v3.step to V05-01-02-01 - X axis motor mount.step
    [V05-01-02-01 - X axis motor mount.step]
2021-07-20 Rename V05-01-02-02 - X axis motor srengthener v5.step to V05-01-02-02 - X axis motor srengthener.step
    [V05-01-02-02 - X axis motor srengthener.step]
2021-07-20 Rename V05-01-03-01 - Y axis shaft end holder v10.step to V05-01-03-01 - Y axis shaft end holder.step
    [V05-01-03-01 - Y axis shaft end holder.step]
2021-07-20 Rename V05-01-03-02 - Y axis motor mount v10.step to V05-01-03-02 - Y axis motor mount.step
    [V05-01-03-02 - Y axis motor mount.step]
2021-07-20 Rename V05-01-04-01 - Left belt tensioner base v3.step to V05-01-04-01 - Left belt tensioner base.step
    [V05-01-04-01 - Left belt tensioner base.step]
2021-07-20 Rename V05-01-04-02-01 - Belt tensioner base v3.step to V05-01-04-02-01 - Belt tensioner base.step
    [V05-01-04-02-01 - Belt tensioner base.step]
2021-07-20 Rename V05-03-05-02 - optical endstop trigger v5.step to V05-03-05-02 - optical endstop trigger.step
    [V05-03-05-02 - optical endstop trigger.step]
2021-07-20 Rename V05-03-01-01 - Z axis beam mount v9.step to V05-03-01-01 - Z axis beam mount.step
    [V05-03-01-01 - Z axis beam mount.step]
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2021-07-20 Rename V05-03-04-01 - Heated bed 250x400 v2.step to V05-03-04-01 - Heated bed 250x400.step
    [V05-03-04-01 - Heated bed 250x400.step]
2021-07-20 Rename V05-03-05-01 - Optical endstop mount v5.step to V05-03-05-01 - Optical endstop mount.step
    [V05-03-05-01 - Optical endstop mount.step]
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2021-07-20 Rename V05-03-03-01-01 - 2020 to 2060 mount v3.step to V05-03-03-01-01 - 2020 to 2060 mount.step
    [V05-03-03-01-01 - 2020 to 2060 mount.step]
2021-07-20 Rename V05-03-02-01 - Z axis motor mount v2.step to V05-03-02-01 - Z axis motor mount.step
    [V05-03-02-01 - Z axis motor mount.step]
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2021-07-20 Fixed V05-01-04-02-02 - Belt tensioner knob
2021-07-21 Updated main assembly and BOM to v0.5.37
    - Added X axis optical endstop
    - Fixel Z axis position
    [BOM v0.5.4-alpha.ods, V05-01-06-01 - X axis mechanical endstop mount.step, V05-01-06-01 - X axis mechanical endstop mount.stl]
2021-07-21 Rename V05-03-05-02 - optical endstop trigger.step to V05-03-05-02 - Z axis optical endstop trigger.step
    [V05-03-05-02 - Z axis optical endstop trigger.step]
2021-07-21 Rename V05-03-05-01 - Optical endstop mount.step to V05-03-05-01 - Z axis optical endstop mount.step
    [V05-03-05-01 - Z axis optical endstop mount.step]
2021-07-21 Rename V05-03-05-02 - optical endstop trigger.stl to V05-03-05-02 - Z axis optical endstop trigger.stl
    [V05-03-05-02 - Z axis optical endstop trigger.stl]
2021-07-21 Rename V05-03-05-01 - Optical endstop mount.stl to V05-03-05-01 - Z axis optical endstop mount.stl
    [V05-03-05-01 - Z axis optical endstop mount.stl]
2021-07-21 Minor fixes in BOM
    [BOM v0.5.4-alpha.ods]
2021-07-24 Rename V05-01-04-02-01 - Belt tensioner base.step to V05-01-04-02-01 - Belt tensioner slider.step
    [V05-01-04-02-01 - Belt tensioner slider.step]
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2021-08-03 BOM updated to v0.5.5-alpha
    Corner vertical profile length calculations fixed
    [BOM v0.5.1-alpha.ods, BOM v0.5.2-alpha.ods, BOM v0.5.3-alpha.ods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]
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2021-08-27 Minor changes
    - Removed parts sub-folders from /parts/step and /parts/stl
    - Minor changes in BOM
    [BOM v0.5.6-alpha.ods, V05-01-01-01-01 - Y axis carriage base.step, V05-01-01-01-01 - Y axis carriage base.stl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]
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2021-10-27 Bugs fixed
    [V06-01-05-01 - Right belt tensioner base.step, V06-01-05-01 - Right belt tensioner base.stl]
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2021-10-27 Minor fixes
    [BOM v0.6.3-alpha.ods, V06-03-03-01-04 - 2020 to 2020 mount.step, V06-03-03-01-04 - 2020 to 2020 mount.stl]
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2021-11-15 Issue fix
    fixed issues: #33 #34 #35 #36 #37 #38
    Updated stock BOM settings
    [BOM v0.6.4-alpha.ods, BOM v0.6.5-alpha.ods, V06-03-03-01-04 - 2020 to 2020 mount.step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]
2021-11-23 Fixed #41
    [V05-03-01-01 - Z axis beam mount.step, V06-03-01-01 - Z axis beam mount.step, V06-03-01-01 - Z axis beam mount.stl]
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2022-01-14 5020 fan duct rework
    [V06-01-01-02-02(L) - BMG e3d v6 5020 fan duct.step, V06-01-01-02-02(L) - BMG e3d v6 5020 fan duct.stl, V06-01-01-02-02(R) - BMG e3d v6 5020 fan duct.step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]
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2022-04-04 Update BOM v0.7.1.ods
    Fixed synchro shaft length
    [BOM v0.7.1.ods]
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2022-04-29 Исправлена длина продольной балки рамы стола
    [BOM v0.7.3.ods]
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2022-06-10 Обновление до версии 0.7.2b
    Исправлены ошибки генерации зашивки для 4 стоек.
    Файл взят из чата Vostok.
2022-08-14 Added missing parts and updated BOM
    [BOM v0.7.3b.ods, V07-04-10-01 - Back door lock.stp]
